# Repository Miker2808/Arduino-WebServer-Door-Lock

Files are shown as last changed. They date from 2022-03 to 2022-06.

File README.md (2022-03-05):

# Arduino Web Server Door Lock

---
## Introduction

### <ins>Behind the project</ins>:

This is a showcase project I've made as a request, while doing this project I learnt a lot new, this project will contain everything required to replicate the exact setup. but, can also be used to learn a lot about arduino, especially the new very powerful Arduino Nano 33 IoT.

### <ins>About the project</ins>:

This project is a door lock, commonly used in work offices. The doorlock uses the Arduino Nano 33 IoT as the main computer for the doorlock, it manages the database of allowed users, stores the door password, reads fingerprint sensor feedback and touchscreen feedback to determine when and whether to unlock the door. Additionally to these tasks, the main access point of the doorlock is a webserver that can be accessed by writing the arduino's IP address in any browser. Through the web gui, the user can change touchscreen door password, assign new fingerprints and corresponding owner name, and revoke fingerprint access if necessary, and to remotely unlock the door from a distance if required. The locking mechanism is a basic electromagnetic lock that magentises when the door is in "locked" state and demagnetises when the door is unlocked.

---
## Features

### <ins>Door Lock WebServer</ins>:

The main feature of this project, is the webserver, which is the Arduino Nano 33 IoT. The arduino holdes multiple features, being the central unit for handling all the operations and simultaniously acting as a webserver.

#### <ins>Main Page</ins>:

Main Web Page

The main page, consists of choosing options, designed to be comfortable to use both 
on computers and on mobile.

#### <ins>Enroll New User</ins>:

Enroll New User

Enrollment of new users is done by assigning an integer ID from 1 to 50
and a name of the fingerprint owner.
The ID can be used later to remove the fingerprint from the system. The name will be displayed
with a welcoming sign on the touchscreen when a user enters the using a fingerprint
The table under the instructions will contain the list of already assigned ID's and matching names. the data is fetched from the arduino, and is kept in the device after shutting down the arduino as emulated EEPROM using flash.

#### <ins>Remove user</ins>:

Delete User

Assigning ID will remove the user from the system, the table will contain all the users and their ID's.

#### <ins>Changing Passwords</ins>:
Change Password

This window allows changing passwords, one for the web gui login page, another for the doorlock touch screen pin.
The web password can characters and numbers, while the door password will hold only integers.

>All the data handling is done using custom structs built to hold the data, and then stored in the arduino as emulated ROM.

---
## The server structure

### <ins>The Setup</ins>:
The arduino nano 33 iot, which acts as the webserver works in the following order:
1. <ins>Setup</ins>: The arduino will initialize by checking the flash memory if a database exists
    with the "not_first_run" flag raised or not.
    If the flag is False, the server will create a database struct and write it to the flash.
    The server will assign default web and door password which can be changed on the web gui.

    After the database setup, the arduino will proceed to attempt wifi connection. on successful connection the arduino will continue to the loop. The arduino will have 3 connection attempts before switching to offline mode, which hold the same function as the online mode but without the server listeing to wireless connections. The fingerprint and touch keypad will continue to function as usual.

2. <ins>Lock Counter</ins>:
    The arduino cycles at fixed delay. Because having the door open exactly for 5 seconds is not very important and we can allow error margin of half a second, having a fixed delay allows us to count time by cycles rather than accessing the internal clock and running delta's. the door lock couter will enable the magnetic lock (thus, locking the door) when it reaches 0, if the decides to unlock the door, it'll set the counter to 100, therefore allowing 5 seconds of unlocked time, with a slight error depending on the loop.

3. <ins>Fingerprint handler</ins>:
   The next step will be to give a window to the fingerprint serial connection to see if we got a finger placement on the fingerprint sensor. If we indeed, do have fingerprint placement, the function will proceed to checking if such a fingerprint was assigned and is in the system. The hash of the fingeprint is done internally in the fingerprit sensor, the adafruit library will return only the ID of the hash if it is positive. the number of prints possible in the sensor is dependent ont he sensor, the one in use allows up to 80, some allow 300 and more.
   Furthermore, if the fingerprint sensor does have a positive ID, the server will compare its ID with the database ID to find a matching name, if it exists it will send the name to the touchscreen arduino for a welcoming message. Otherwise, nothing will happen.

4. <ins>Touchscreen handler</ins>:
   This time, the touchscreen receives time window to read if we have password input from the touchscreen. On positive password match, the server will send a welcoming message for a guest.

5. <ins>Web server handling</ins>:
   The main part of the loop, most of the time it is not used, but is of the most importance beacuse of how fragile it is. The webserver will read for available bytes from the wireless module buffer, if available will will parse the data by lines using hand made http parser. The parser will check the message and assign the data to a http struct that simplifies the construction of the data, if GET is received the method is assinged as GET, for POST, assigned POST. if POST http method is given, the parser will assign to the data varialbe as well.
   
   After successful parsing, the webserver will check if POST or GET methods were given and act accordingly, this allows moving between pages. As a small security measure, the movement between pages is done as a POST method, any GET method will give only the login page.

><ins> about security: </ins>
The webserver was not designed for maximum security (maybe not even decent) because of the difficulty of using HTTPS with arduino and the limited time I had (The whole project was done in 2-3 months). 

---
## The Touchscreen Structure

The arduino uno with adafruit touch and LCD screen shield works as follows:
1. <ins>The Setup:</ins> The setup is very simple, create serial connection with the server     arduino, and connect to the touch screen and lcd. the "reset_screen()" function will draw the default keypad.

2. <ins>Screen Backlight Timer:</ins> Just like with the webserver arduino, number of loop iterations is used to know when to turn off the backlight, when the counter reaches 0, the backlight will turn off.
   
   `Note: the backlight requires soldering two points on the shield, refer to the adafruit manual for more information`
3. <ins>Arduino Server Commands Handler</ins>: This function will check the serial, if data is available it will parse it and choose what to do, from showing welcoming message to a positive fingerprint ID, to showing steps for new fingerprint assignments.
4. <ins>Touch handling</ins>: The last part is to check the touchscreen for touched X,Y positions, only the latest X,Y is taken. The arduino will loop for all 3 by 4 keys and check their bounds, if touched they will change the color of the button touched. The process will continue until the button is released, once released on the X,Y position, the pressed button is processed and if 0-9 digits is pressed, the number is appended to the password input. on DEL, the last digit is removed, on ENT, the password digit is sent to the arduino server.
if no input is given in 5 seconds, the password is reset and the LCD turns the backlight off.

> Note: When the backlight is off, the touch will continue to function to create "wake up" effect.

---
## Bill of materials

The following table lists all the equipment I used for the project.
The magnetic lock can be anything that works as On/Off switch and works with 12V.

|Equipment |Quantity| LINK |
|---|:---:|:---:|
|Arduino Uno R3 |1|[Official Arduino](https://store.arduino.cc/products/arduino-uno-rev3)|
|Arduino Nano 33 IOT |1|[Official Arduino](https://store.arduino.cc/products/arduino-nano-33-iot)|
|3.3V Switching Relay. **Any 3.3V relay will work**|1|[Aliexpress](aliexpress.com/item/1005001567474787.html)|
|5V/5.5A Reducing Voltage Regulator Model: D36V50F5|1 |[Pololu](https://www.pololu.com/product/4091)|
|3.3V/3.6A Reducing Voltage Regulator Model: D36V28F3|1 |[Pololu](https://www.pololu.com/product/3781)|
|12V/3A AC to DC Power Supply | 1 | *Bought locally, may differ for every country*|
|Ultra-Slim Round Fingerprint Sensor and 6-pin Cable| 1| [Adafruit](https://www.adafruit.com/product/4750)|
|2.8" TFT Touch Shield for Arduino with Capacitive Touch| 1 | [Adafruit](https://www.adafruit.com/product/1947)|
|Magnetic Door Lock, Inter/Exter, 1200 lbs. **Any 12V lock will work**| 1| [Octopart](https://octopart.com/del12003-storm+interface-50419236)|
| 2mm zipties `The 3d printed cases use zipties.`|100| *Bought locally*|
> Does not include 3d Print filament, 3D printer, Electrical Wires, and connectors.
> The choice is up to you, any connectors will work, but Ethernet cable will be the best for the power and data transmission from the arduino inner side box to the outer side box.

---
## CAD and Wiring

The following images show the structure of the equipment. The project consits of two main parts.

<ins>**The inner encasement**</ins>:
The inner encasement holds the arduino server, voltage regulators, door opening button, and the switching relay. It should be placed inside the locked room to avoid tampering.

<ins>The inner encasement</ins>

Inner encasement

<ins>Closed inner encasement</ins>

Closed Inner encasement

<ins>Wiring Diagram</ins>

Inner encasement wiring diagram

> The repository encludes `dxf` files which allow seeing the wiring in a variable zoom.

<ins>**The outer encasement**</ins>:
The outer encasement holds the arduino uno with the touch screen and the fingerprint sensor.
A cable should be used to connect the power and communication wirings. Personally, I used a basic ethernet cat6 cable both for data and power, and it works flawlessly.

<ins>The outer encasement</ins>

Outer encasmenet

> The repository includes `dxf` file with the wiring diagram.

> All the CAD files are available in the CAD directory, additional electrical components are available for download as solidworks files, due to their size. Some of the components are 3rd party from `Grabcad.com`. The following solidworks components can be downloaded from [here](https://mega.nz/file/0AtWTJyQ#VIRockYbuOe-4gDbsIgEDWmeqSzSNvUkM9Bv7lscPkU).

---
## Small PC Script
The repository includes a small python script (up to 10 lines of code) that can be used to send an http request to the webserver to open the door from computers on the same network. It's used to allow people from inside to continue with their laziness and avoid standing up to open the door when someone is knocking.

---
## Showcase Videos
<ins>Password keypad demo</ins>:

Showcase password video

<ins>Fingerprint demo</ins>:

Showcase fingerprint video

---
## Licensing
The project is open for use as followed by the GNU General Public License V3.
The liecnse file is included in the repository.

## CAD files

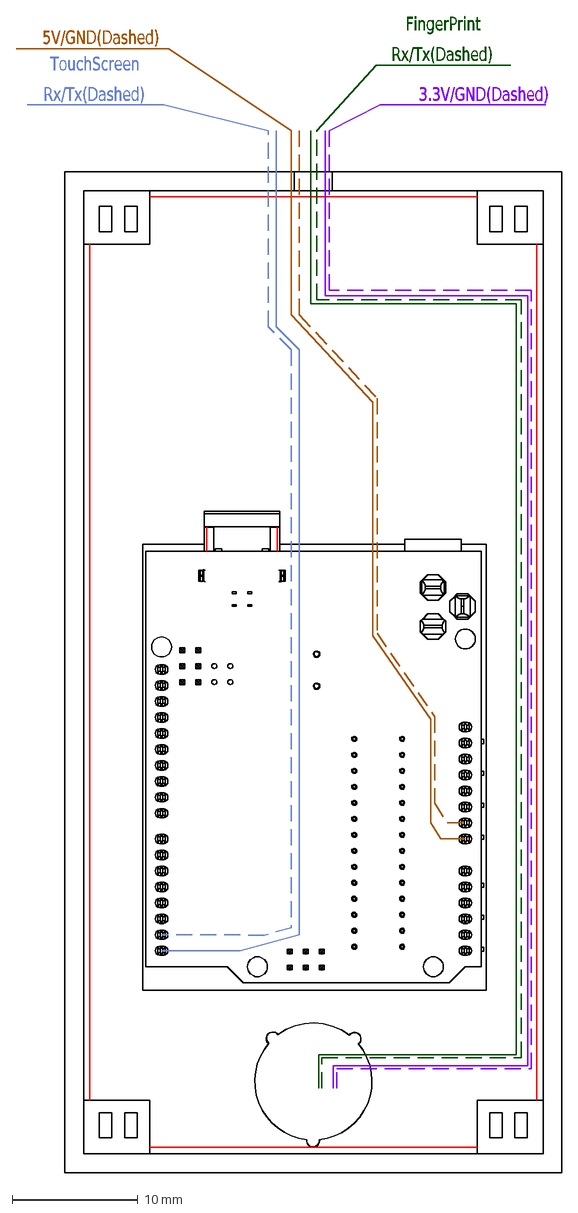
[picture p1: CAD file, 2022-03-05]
CAD/OuterEDiagram.DXF
3.3V/GND(Dashed)
FingerPrint
Rx/Tx(Dashed)
TouchScreen
5V/GND(Dashed)

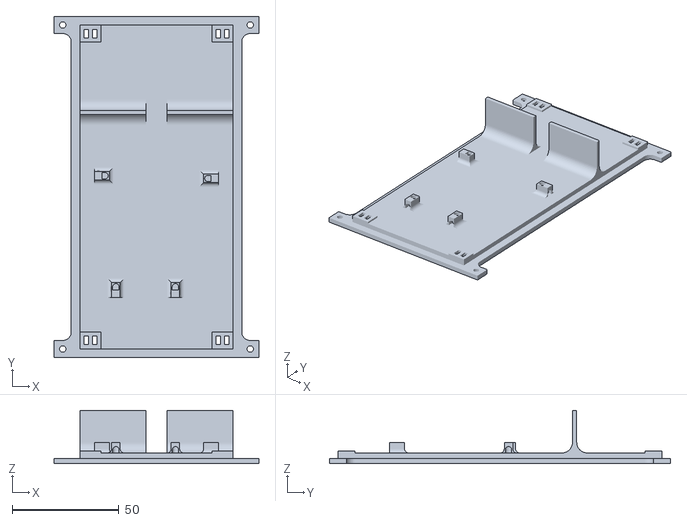
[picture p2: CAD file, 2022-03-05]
CAD/STLs/door-lock-outside-plate.STL
96.0 x 160.0 x 25.0

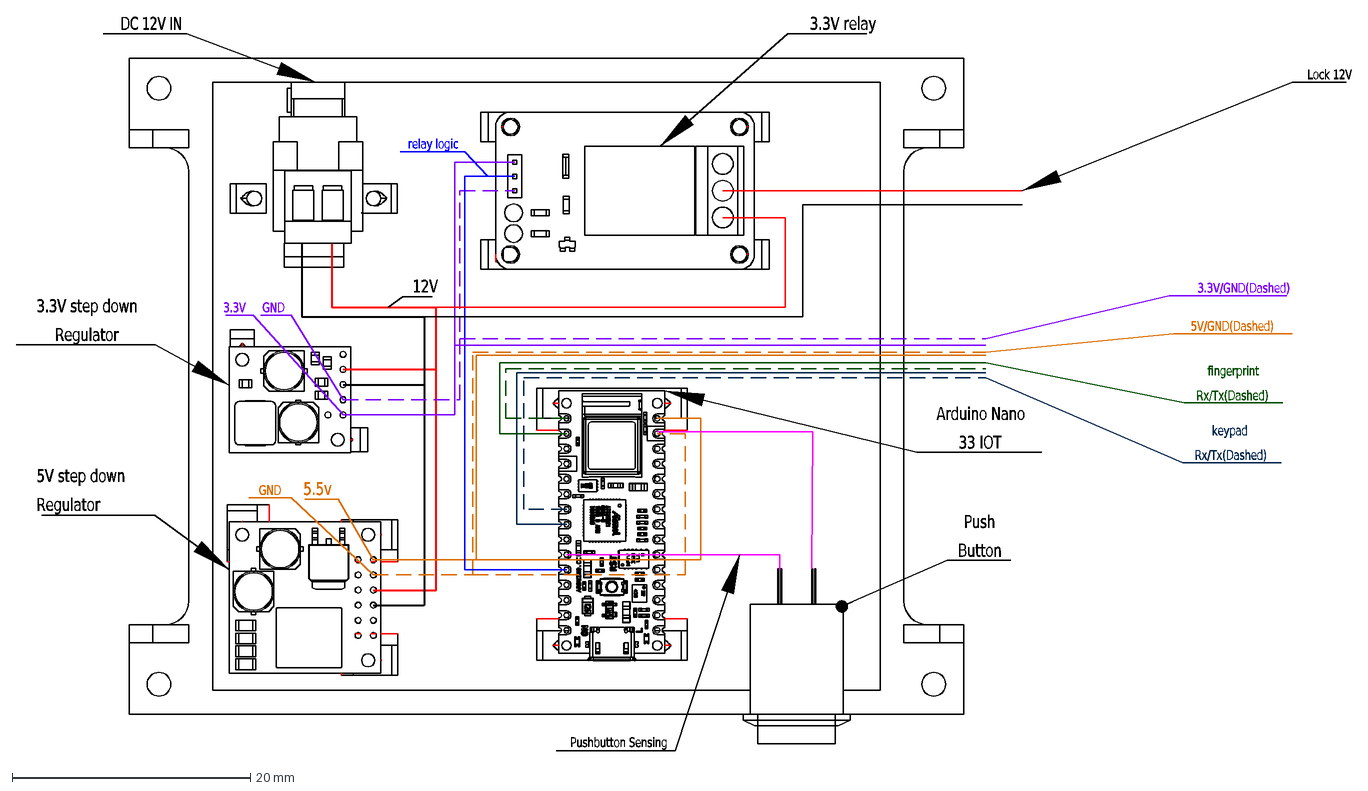
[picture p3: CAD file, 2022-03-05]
CAD/InnerEDiagram.DXF
3.3V relay
DC 12V IN
3.3V step down
Regulator
5V step down
Arduino Nano
33 IOT
Push
Button
12V
5.5v
keypad
Rx/Tx(Dashed)
fingerprint
GND
5V/GND(Dashed)
3.3V
3.3V/GND(Dashed)
Lock 12V
Pushbutton Sensing
relay logic

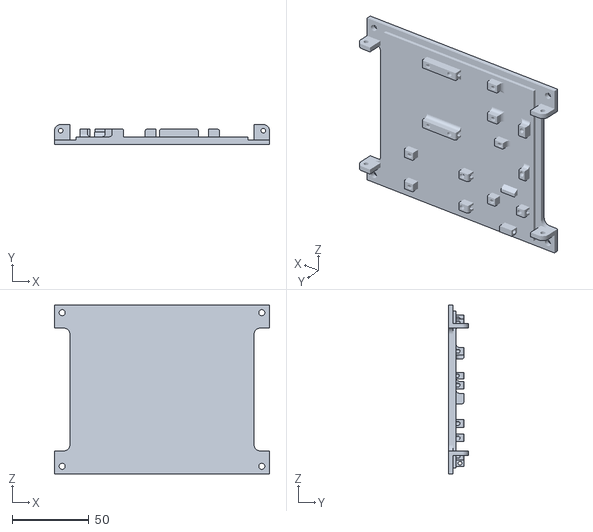
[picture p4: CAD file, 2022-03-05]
CAD/STLs/doorlock-inside.STL
140.0 x 13.0 x 110.0

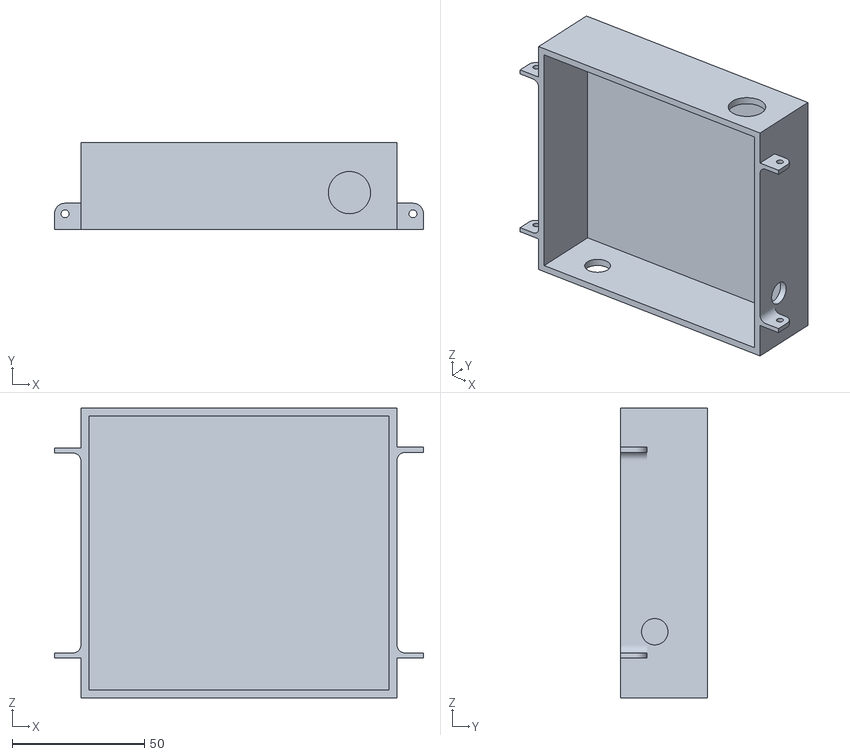
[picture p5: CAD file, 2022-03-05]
CAD/STLs/doorlock-inside-cover.STL
139.5 x 33.0 x 109.5

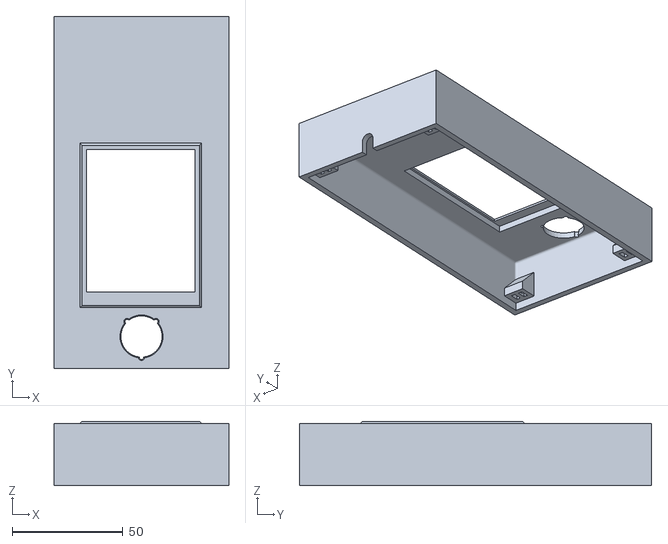
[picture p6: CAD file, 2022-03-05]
CAD/STLs/doorlock-outside-cover.STL
79.0 x 159.0 x 29.0

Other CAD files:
CAD/Parasolid/door-lock-outside-plate.x_t
CAD/Parasolid/doorlock-inside-cover.x_t
CAD/Parasolid/doorlock-inside.x_t
CAD/Parasolid/doorlock-outside-cover.x_t

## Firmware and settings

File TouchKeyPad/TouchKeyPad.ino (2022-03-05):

// Software written by: Michael Pogodin
// Contact: miker2808@gmail.com
// Last Edit: 24/12/2021

#include <Adafruit_GFX.h>    // Core graphics library
#include <SPI.h>
#include <Wire.h>      // this is needed even tho we aren't using it
#include <Adafruit_ILI9341.h>
#include <Adafruit_STMPE610.h>

#include <Fonts/FreeMonoBold12pt7b.h>

// This is calibration data for the raw touch data to the screen coordinates
#define TS_MINX 150
#define TS_MINY 130
#define TS_MAXX 3800
#define TS_MAXY 4000

// The STMPE610 uses hardware SPI on the shield, and #8
#define STMPE_CS 8
Adafruit_STMPE610 ts = Adafruit_STMPE610(STMPE_CS);

// The display also uses hardware SPI, plus #9 & #10
#define TFT_CS 10
#define TFT_DC 9
Adafruit_ILI9341 tft = Adafruit_ILI9341(TFT_CS, TFT_DC);

#define BLACK      0x0000
#define BLUE       0x001F
#define RED        0xF800
#define GREEN      0x07E0
#define CYAN       0x07FF
#define MAGENTA    0xF81F
#define YELLOW     0xFFE0
#define WHITE      0xFFFF
#define DARK_GRAY  0x1111
#define LIGHT_GRAY 0XCCCC

// used to remember what key was touched last iteration
int pressed_j = 0;
int pressed_i = 0;
char pressed_char = 0;
bool was_pressed = false;
String input_pass = "";
int stay_awake_counter = 250; // turn screen off when reaching 0

void draw_keypad_char(int i, int j, int input_char, int color_block, int color_text, int text_size = 2) {
  tft.fillRect(11 + j * 75, 75 + i * 60, 70, 55, color_block);
  tft.drawRect(11 - 2 + j * 75, 75 - 2 + i * 60, 70 + 2, 55 + 2, color_text);
  tft.drawChar(11 + 20 + j * 75, 75 + 42 + i * 60, input_char, color_text, 0, text_size);

}

void draw_keypad_string(int i, int j, int color_block, int color_text, String input_text, int text_size = 1) {
  tft.fillRect(11 + j * 75, 75 + i * 60, 70, 55, color_block);
  tft.drawRect(11 - 2 + j * 75, 75 - 2 + i * 60, 70 + 2, 55 + 2, BLACK);
  tft.setCursor(11 + 12 + j * 75, 75 + 35 + i * 60);
  tft.setTextColor(color_text);
  tft.setTextSize(text_size);
  tft.print(input_text);
}

void reset_screen() {
  // Clean the screen and rest to default look

  int screen_width = tft.width();
  int screen_height = tft.height();

  tft.setRotation(0);

  // fill the screen with black
  tft.fillScreen(WHITE);

  char count_char = 49;
  for (int i = 0; i < 4; i++) {
    for (int j = 0; j < 3; j++) {
      if (i == 3) {
        if (j == 0) {
          draw_keypad_string(i, j, BLACK, WHITE, "DEL", 1);

        }
        else if (j == 1) {
          draw_keypad_char(i, j, 48, BLACK, WHITE);

        }
        else if (j == 2) {
          draw_keypad_string(i, j, BLACK, WHITE, "ENT", 1);
        }
      }
      else {
        draw_keypad_char(i, j, count_char, BLACK, WHITE);
        count_char += 1;
      }
    }
  }
}

void screenWrongPassword() {
  // create image that shows invalid password
  tft.fillScreen(WHITE);
  tft.setCursor(20, 150);
  tft.setTextColor(BLACK);
  tft.setTextSize(2);
  tft.print("INVALID");
  tft.setCursor(10, 200);
  tft.setTextColor(BLACK);
  tft.setTextSize(2);
  tft.print("PASSWORD");
  delay(2500);
  reset_screen();
  delay(500);
  stay_awake_counter = 250;

}

void screenCommError() {
  // create image that shows Comm Error
  tft.fillScreen(WHITE);
  tft.setCursor(60, 100);
  tft.setTextColor(BLACK);
  tft.setTextSize(2);
  tft.print("Comm");
  tft.setCursor(50, 150);
  tft.setTextColor(BLACK);
  tft.setTextSize(2);
  tft.print("Error");
  tft.setCursor(30, 250);
  tft.setTextColor(BLACK);
  tft.setTextSize(1);
  tft.print("C:0x465F550A");
  delay(2500);
  reset_screen();
  delay(500);
}

void screenDebugPrint(String input_str) {
  // create image that shows the input string (For debugging)
  tft.fillScreen(WHITE);
  tft.setCursor(10, 100);
  tft.setTextColor(BLACK);
  tft.setTextSize(1);
  tft.print(input_str);
  
}

void screenSetFinger(String finger_action){
  tft.fillScreen(WHITE);
  tft.setCursor(20, 140);
  tft.setTextColor(BLACK);
  tft.setTextSize(2);
  tft.print(finger_action);
  tft.setCursor(20, 200);
  tft.setTextColor(BLACK);
  tft.setTextSize(2);
  tft.print("FINGER");
  stay_awake_counter = 500;
}

void screenSetFingerResult(bool set_finger_result){
  tft.fillScreen(WHITE);
  tft.setTextColor(BLACK);
  tft.setTextSize(1);
  tft.setCursor(65, 150);
  tft.print("FINGER");
  tft.setCursor(50, 180);
  tft.print("ENROLLMENT");
  tft.setCursor(60, 210);
  tft.fillRect(48, 193, 129, 24, BLACK);
  tft.fillRect(50, 195, 125, 20, WHITE);
  if(set_finger_result == true){
    tft.print("FINISHED");
  }
  else{
    tft.print("FAILED");
  }
  
  delay(3000);
  reset_screen();
  delay(500);
  return;
  
}

void screenValidUser(String user_name) {
  // create image that shows valid finger with name ("Welcome {user_name}")
  // create image that shows invalid password
  
  tft.fillScreen(WHITE);
  tft.setCursor(20, 140);
  tft.setTextColor(BLACK);
  tft.setTextSize(2);
  tft.print("WELCOME");
  tft.fillRect(0, 145, 240, 3, BLACK);

  // change cursor so text of name is in the middle
  if(user_name.length() <= 8){
    int cursor_x = 120 - ((user_name.length()/2)*28);
    tft.setCursor(cursor_x, 200);
    tft.setTextColor(BLACK);
    tft.setTextSize(2);
    tft.print(user_name);
    delay(5000);
    reset_screen();
    delay(500);
    return;
  }
  else{
    int space_index = 0;
    for(int i = 0; i < user_name.length(); i++){
      if(user_name[i] == ' ' or user_name[i] == '+'){
        space_index = i;
        break;
      }
    }
    String first_name = user_name.substring(0, space_index);
    String surname = user_name.substring(space_index+1);
    int cursor_x_first = 120 - ((first_name.length()/2)*28);
    int cursor_x_surname = 120 - ((surname.length()/2)*15);
    // print first name
    tft.setCursor(cursor_x_first, 200);
    tft.setTextColor(BLACK);
    tft.setTextSize(2);
    tft.print(first_name);
    // print surname
    tft.fillRect(0, 210, 240, 30, BLACK);
    tft.setCursor(cursor_x_surname, 230);
    tft.setTextColor(WHITE);
    tft.setTextSize(1.5);
    tft.print(surname);
    delay(5000);
    reset_screen();
    delay(500);
    return;
  }
}

void handleReceivingCommand() {
  if (Serial.available() > 0) {
    String received_input = Serial.readStringUntil('\n');
    if(received_input.startsWith("PSWD:GOOD")) {
      digitalWrite(3, HIGH);
      screenValidUser("GUEST");
    }
    else if(received_input.startsWith("PSWD:BAD")) {
      digitalWrite(3, HIGH);
      screenWrongPassword();
    }

    else if(received_input.startsWith("PSWD:LOCK")) {
      digitalWrite(3, HIGH);
      screenCommError();
    }

    else if (received_input.startsWith("FNGR:")) {
      digitalWrite(3, HIGH);
      String user_name = received_input.substring(5);
      screenValidUser(user_name);
    }

    else if(received_input.startsWith("SMSG:SETFNGR-PLACE")){
      screenSetFinger("PLACE");
    }
    else if(received_input.startsWith("SMSG:SETFNGR-RELEASE")){
      screenSetFinger("RELEASE");
    }
    else if(received_input.startsWith("SMSG:SETFNGR-FINISH")){
      screenSetFingerResult(true);
    }
    else if(received_input.startsWith("SMSG:SETFNGR-FAILED")){
      screenSetFingerResult(false);
    }
    
  }
  Serial.flush();
}

void setup() {

  // delay to fix tft not initiating without USB
  delay(2000);

  pinMode(3, OUTPUT);
  digitalWrite(3, HIGH);
  // object for LCD screen (To control pixels)
  tft.begin();

  // object for touch controller (To read touch input)
  if (!ts.begin()) {
    //Serial.println("Couldn't start touchscreen controller");
    // set reboot
  }
  //Serial.println("Touchscreen started");

  tft.setFont(&FreeMonoBold12pt7b);

  reset_screen();

  Serial.begin(115200);

}


void loop()
{
  if(stay_awake_counter > 0){
    stay_awake_counter -= 1;
    digitalWrite(3, HIGH);
  }
  if(stay_awake_counter <= 0){
    // Turns the screen OFF (physically turn off backlight), touch will still work
    tft.fillScreen(BLACK);
    digitalWrite(3, LOW);
  }
  handleReceivingCommand(); // used to check the serial to know if any commands arrived
  //TS_Point p = ts.getPoint();
  // See if there's any  touch data for us, cleans buffer as well
  if (!ts.bufferEmpty()) {
    digitalWrite(3, HIGH);
    if(stay_awake_counter <= 0){
      reset_screen();
      TS_Point p = ts.getPoint(); // to clean buffer
      stay_awake_counter = 250;
      input_pass = "";
      delay(500);
      return;
    }
    stay_awake_counter = 250;
    
    char pressed_value = 0;
    // Retrieve a point
    TS_Point p = ts.getPoint();

    // Scale from ~0->4000 to tft.width using the calibration #'s
    p.x = map(p.x, TS_MINX, TS_MAXX, 0, tft.width());
    p.y = map(p.y, TS_MINY, TS_MAXY, 0, tft.height());

    char count_char = 49;
    // The loop checks if one of the 12 keys was pressed.
    // i = col
    // j = row
    for (int i = 0; i < 4; i++) {
      for (int j = 0; j < 3; j++) {
        if (p.x > (11 + j * 75) and p.x < (11 + j * 75 + 70) and p.y > (75 + i * 60) and p.y < (75 + i * 60 + 55)) {
          if (i == 3) {
            if (j == 0) { // check if the Delete "<" button was pressed
              draw_keypad_string(i, j, WHITE, BLACK, "DEL", 1);
              pressed_j = j;
              pressed_i = i;
              pressed_char = 60; // equal to char '<'
              was_pressed = true;
              break;
            }
            else if (j == 1) { // check if the 0 button was pressed
              draw_keypad_char(i, j, 48, WHITE, BLACK);
              pressed_j = j;
              pressed_i = i;
              pressed_char = 48;
              was_pressed = true;
              break;
            }
            else if (j == 2) { // check if the SEND ">" button was pressed
              draw_keypad_string(i, j, WHITE, BLACK, "ENT", 1);
              pressed_j = j;
              pressed_i = i;
              pressed_char = 62; // equal to char '>'
              was_pressed = true;
              break;
            }
          }
          else { // otherwise
            draw_keypad_char(i, j, count_char, WHITE, BLACK);
            // reset parameters if pressed
            pressed_j = j;
            pressed_i = i;
            pressed_char = count_char;
            was_pressed = true;
            break;
          }
        }
        count_char += 1;
      }
    }

    // continue if pressed
  }

  else {
    if (was_pressed) {
      // check what key was pressed to know how to restore its view (reset_screen() is too slow)
      if (pressed_i == 3 and (pressed_j == 0 or pressed_j == 2)) {
        if (pressed_j == 0) {
          draw_keypad_string(pressed_i, pressed_j, BLACK, WHITE, "DEL", 1);
        }
        else if (pressed_j == 2) {
          draw_keypad_string(pressed_i, pressed_j, BLACK, WHITE, "ENT", 1);
        }
      }
      else {
        draw_keypad_char(pressed_i, pressed_j, pressed_char, BLACK, WHITE);
      }

      // on "DEL" released:
      if (pressed_i == 3 and pressed_j == 0) {
        //mask the input with a white rectangle
        tft.fillRect(0, 0, 240, 75, WHITE);
        // remove one character from the password
        input_pass.remove(input_pass.length() - 1);
        // print the new password again
        tft.setCursor(30, 50);
        tft.setTextColor(BLACK);
        tft.setTextSize(2);
        tft.print(input_pass);
      }
      // on "ENT" released:
      else if (pressed_i == 3 and pressed_j == 2 and input_pass.length() > 0) {
        Serial.println(String("PSWD:" + input_pass));
        input_pass = "";
        //mask the input with a white rectangle
        tft.fillRect(0, 0, 240, 75, WHITE);
        //reset_screen();
        delay(50);
      }
      // on any other key released:
      else {
        if (input_pass.length() < 6 and pressed_char != '<' and pressed_char != '>') {
          input_pass += pressed_char;
          tft.setCursor(30, 50);
          tft.setTextColor(BLACK);
          tft.setTextSize(2);
          tft.print(input_pass);
        }
      }
      was_pressed = false;
    }
    // continue no touch received
    // if data is available in buffer, do accordingly
    //handleReceivingCommand();
  }
  // out of touch bounds

  delay(20);
}

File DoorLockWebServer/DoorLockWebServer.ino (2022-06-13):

//MAC address: A4:CF:12:8B:D6:34

// Software written by: Michael Pogodin
// Contact: miker2808@gmail.com
// Last Edit: 24/12/2021

#include <SPI.h> // Came with Wifi libraries
#include <WiFiNINA.h> // used for wifi
#include <FlashStorage.h> // used to store user database and passwords
#include <Arduino.h> // used for hardware serial (communicate with touchpad arduino)
#include "wiring_private.h" // used for hardware serial (communicate with touchpad arduino)
#include <Adafruit_Fingerprint.h>

// struct of the http request
struct httpRequest{
  String httpmethod= ""; // returns line of GET or POST
  String httpredirect = ""; // returns direction of GET or POST
  String data = ""; // returns data if POST
  String username = ""; // from authorization
  String password = ""; // from authorization
};

// struct of the database
struct dataBase{
  bool not_first_run;
  bool lockdown_mode;
  int door_password;
  char web_password[25];
  char user_name[52][25]; 
};

//// used for the hardware serial
// used to assign pin 5,6 as hardware serial
Uart keypadSerial (&sercom0, 5, 6, SERCOM_RX_PAD_1, UART_TX_PAD_0);
// Attach the interrupt handler to the SERCOM
void SERCOM0_Handler()
{
    keypadSerial.IrqHandler();
}


/////// Connecting wifi information (keyIndex is not used for WPA)
char ssid[] = "";    // your network SSID (name)
char pass[] = "";    // your network password (use for WPA, or use as key for WEP)
int keyIndex = 0;                // your network key index number (needed only for WEP)

int wifi_reconnect_clock = 0; // when failed reconnection and wifi is off, attempt when reaches 0

int status = WL_IDLE_STATUS;
WiFiServer server(80);

// define Serial1 (Rx,Tx pins) to fingerSerial (easier for work)
#define fingerSerial Serial1
Adafruit_Fingerprint finger = Adafruit_Fingerprint(&fingerSerial);

// create storage location for the user database and create user_base out of struct
FlashStorage(userBase_storage, dataBase);
dataBase user_base; // initialize structure of user database

void setup() {
  delay(1000);
  // Reassign pins 5 and 6 to SERCOM alt
  pinPeripheral(5, PIO_SERCOM_ALT);
  pinPeripheral(6, PIO_SERCOM_ALT);
  // Start assigned hardware serial
  keypadSerial.begin(115200);
  
  //Initialize serial and wait for port to open:
  Serial.begin(9600);
  finger.begin(57600);

  if (finger.verifyPassword()) {
    Serial.println("Found fingerprint sensor!");
  }
  else{
    Serial.println("Did not find fingerprint sensor!");  
  }
  
  
  // set the digital pin to control opening the door
  pinMode(8, OUTPUT);
  pinMode(LED_BUILTIN, OUTPUT);
  digitalWrite(8, HIGH);

  // assign pin for the physical button responsible for opening the door
  pinMode(7, INPUT_PULLUP);
  
  user_base = userBase_storage.read(); // assign to user_base the data from flash storage
  
  // check if value was already assigned to flash
  if(user_base.not_first_run == false){
    Serial.print("First run after flashing, assigning default passwords - ");
    Serial.println("door: 321321, web:123123");
    // assign values for first setup (after flash)
    user_base.lockdown_mode = false;
    user_base.not_first_run = true;
    user_base.door_password = 321321;
    String default_web_password = "123123";
    default_web_password.toCharArray(user_base.web_password, 25);

    Serial.println("Asigning default User: Admin - ID: 51");
    // assigning default first user: (Protected)
    String default_user_name = "Admin";
    default_user_name.toCharArray(user_base.user_name[51], 25);

    // write the data to flash
    userBase_storage.write(user_base);
  }
  Serial.print("Current assigned passwords: web: ");
  Serial.print(user_base.web_password);
  Serial.print(", door: ");
  Serial.println(user_base.door_password);
  Serial.println("RouterLogin Webserver");

  // check for the WiFi module:
  if (WiFi.status() == WL_NO_MODULE) {
    Serial.println("Communication with WiFi module failed!");
    // don't continue
    while (true);
    // something very problematic here. arduino reset is required
    // TODO: reset arduino module
  }

  String fv = WiFi.firmwareVersion();
  if (fv < WIFI_FIRMWARE_LATEST_VERSION) {
    Serial.println("Wifi fimrware update available. \nPlease upgrade the firmware");
  }

  // Configure device IP addres
   WiFi.config(IPAddress(10, 0, 40, 250));

  // print the network name (SSID);
  Serial.print("Connecting to wifi: ");
  Serial.println(ssid);

  // Create open network. Change this line if you want to create an WEP network:
  for(int i = 0; i < 3; i++){
    status = WiFi.begin(ssid, pass);
    if (status != WL_CONNECTED) {
      Serial.println("Failed connecting to wifi");
      Serial.println("Retrying in 2 seconds:");
      delay(2000);
      Serial.println("Retrying");
    }
    else{
      // wait 5 seconds for connection:
      delay(5000);
    
      // start the web server on port 80
      server.begin();
    
      // you're connected now, so print out the status
      printWiFiStatus();
      break;
    }
  }
  if(status != WL_CONNECTED) {
    Serial.println("Failed connecting to wifi 3/3, going offline mode");
    wifi_reconnect_clock = 72000;
  }
}

int open_door_counter = 0; // close the door when value is 0 or smaller
int lockdown_engaged = false;
int inner_unlock_button_value = 0;
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
